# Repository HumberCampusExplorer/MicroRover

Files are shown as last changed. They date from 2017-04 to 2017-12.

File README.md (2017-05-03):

# Micro Rover
Adapted from [Rick's Trinket Rover](https://github.com/rwinscot/TrinketRover), estimated build time: 3 hours.
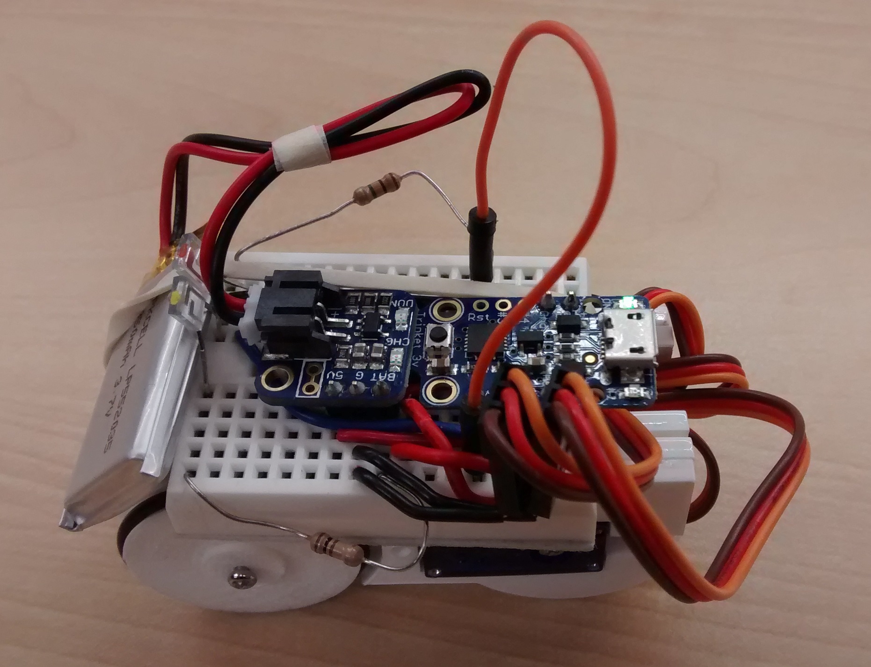
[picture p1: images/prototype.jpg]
Image of Prototype


## Table of Contents
1. [Introduction](https://github.com/six0four/MicroRover#1-introduction)
2. [Bill of Materials and Required Tools](https://github.com/six0four/MicroRover#2-bill-of-materials-and-required-tools)
3. [Instructions](https://github.com/six0four/MicroRover#3-instructions)
4. [Future Development](https://github.com/six0four/MicroRover#4-future-development)

## 1. Introduction
A common introduction to microcontrollers is through the [Lego NXT ROBOTC Curriculum](http://www.education.rec.ri.cmu.edu/previews/robot_c_products/teaching_rc_lego_v2_preview/home/ROBOTC_Curriculum_Outline.pdf). This project aims to use a low cost platform to also explore microcontrollers. Similarly, a small rover is assembled as the vehicle. Currently the small rover moves forward until an object reflects infrared light which triggers it to reverse and turn before continuing forward again.

## 2. Bill of Materials and Required Tools
For a list of materials please see the Excel file in the repository.

Regarding tools, the following are a minimum:
- Safety glasses.
- Soldering iron and lead free solder (to be added to materials list).
- Small side cutting pliers.
- Small Phillips screw driver.

## 3. Instructions
1. Soldering guidance:
	1. Start off by watching some ahort soldering guidance videos: [NASA Jove Project](https://radiojove.gsfc.nasa.gov/telescope/soldering.htm).
	2. Continue by watching some [YouTube Videos](https://www.youtube.com/watch?v=BLfXXRfRIzY&list=PLQ32vZrF5U2lFOJTtZDytBWBYVLNp4RYz).
	3. Be sure to wear safety glasses and consult an expert regarding safety, you can even start at your [local hackerspace](https://wiki.hackerspaces.org/List_of_Hackerspaces).
2. Start by programming the trinket with a blink program prior to soldering to make sure it works.
3. Soldering the headers onto to make sure trinket undamaged.
4. Upload the blink program to the trinket again to make sure it is undamaged.
6, Power the trinket from the power supply. Set the current limit.
4. Test the voltage on the 3.7 V 350 mAh Lithium Ion Polymer 552035 Cell. (Notice from the datasheet that the <a href="https://cdn-shop.adafruit.com/product-files/2750/LP552035_350MAH_3.7V_20150906.pdf">Discharge Cut-off
is 3.0V, the Charging Cut-off is 4.2V, and the Storage Voltage is 3.7-3.85V</a>)
7. Turn on the oscilloscope.
8. Turn on the funtion generator.
9. Disconnect the power supply and connect the 
5. Upload the rover code to the trinket.
6.
7.
8.

Fritzing diagrams needed
Circuit

## 4. Future Development:
- Incorporate multimeter use to check cell.
- Incorporate power supply use as a current controlled alternative to lion cell.
- Incorporate oscilloscope use to view servo motor command signal.
- Incorporate function generator use to create a test control signals.
- Serial communication http://www.ernstc.dk/arduino/tinycom.html to view digitization of infra-red sensor.
- Optimize to stay on desk.
- Optimize to seek dark spaces.
- Optimize for line following.
- Optimize to seek bright spaces and charge via a solar panel.
- Add bluetooth.
- Connect to an Android App that is also connected to Firebase.
- Re-flashing, changing, and removing boot loaders.
- Support for more operating systems.
- Support for more programming languages (Atmel AVR Assembly, ANSI C, Java, Python, IEC 61131-3, javascript, etc.).
- Support for more development environments (AVR-GCC/vi|emacs/AVRdude, Atmel Studio/Visual Studio, etc.).
- Optimize for mapping.
- Communicate with an I2C device as a master
- Communicate with an SPI device.
- Communicate with an I2C device as a slave.
- Communicate with a UART device.
- Communicate via infra-red remote codes.
- Add an H-bridge.
- Add an opto-coupler.
- Add a bidirectional level shifter.
- Modify for DC motors, optical encoders, relays.
- Modify for stepper motors (bipolar and unipolar).
- https://thewanderingengineer.com/2014/08/11/pin-change-interrupts-on-attiny85/
- PID feedback control, fan, thermistor, thermocouple.
- Function generator.
- D to A, PWM.
- A to D, filters.
- Solar cell, photo-resistor.
- Wheatstone bridge, instrumentation amplifier.
- Displays.
- De-bouncing reed switch.
- Emulate a keyboard.
- Playback sound.
- Create a custom PCB with an integrated USB port.
- Shift register, multiplexer.
- RS232, RS485.
- Add a 9-DOF IMU.
- Add MICROCHIP I2C I/O Expander MCP23017.
- Use with http://www.atmel.com/tools/atatmel-ice.aspx and http://www.microchip.com/DevelopmentTools/ProductDetails.aspx?PartNO=ATPOWERDEBUGGER
- Design shell for injection molding.
- Bar/QR code scanners, RFID, magnetic strip, fingerprint readers.
- Add SJA1000/MCP2515 for CAN.
- http://perso.uclouvain.be/fstandae/lightweight_ciphers/
- http://www.instructables.com/id/Optical-Mouse-Odometer-for-Arduino-Robot/?ALLSTEPS
- Currently the project uses a low cost, low power microcontroller from Microchip (Atmel). It could be expanded to be suitable for offerings from other companies such as:
	- Broadcom
	- National Instruments
	- Philips
	- Qualcomm (including NXP, Motorola, and Freescale)
	- Texas Instruments
	- Xilinx
	- Altera
	- Analog Devices
	- Cypress
	- Exynos (Samsung)
	- Infineon Technologies
	- Nordic Semiconductor
	- ON Semiconductor (including Fairchild)
	- Renesas Electronics (including NEC, Hitatchi, Mitsubishi)
	- SGS-THOMSON Microelectronics
	- Silicon Labs

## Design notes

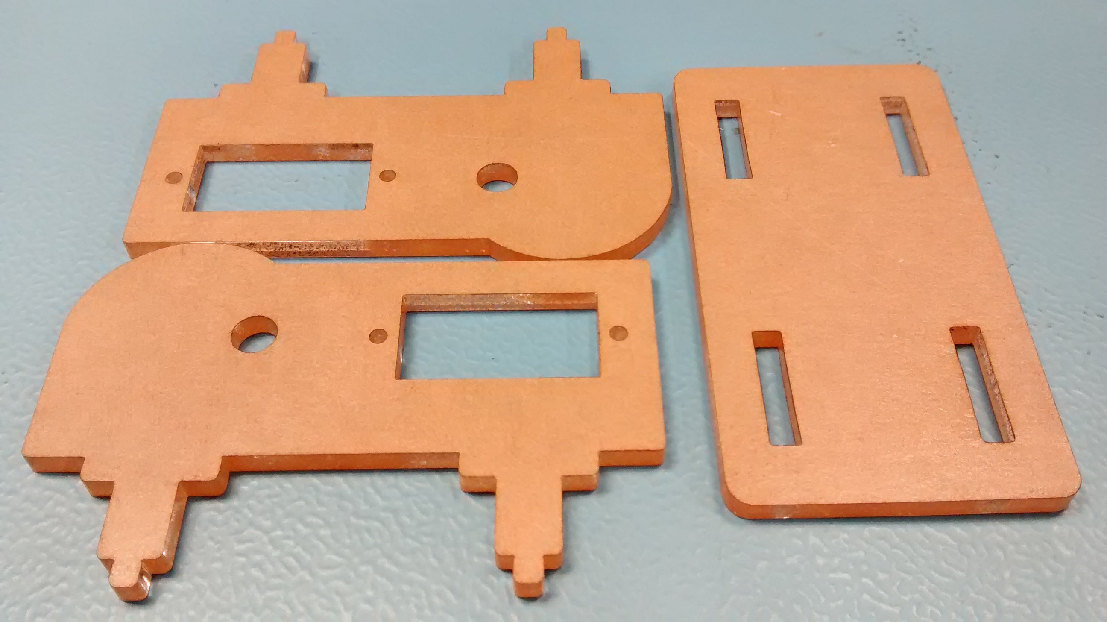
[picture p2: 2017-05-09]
images/1.13laserchassis.jpg

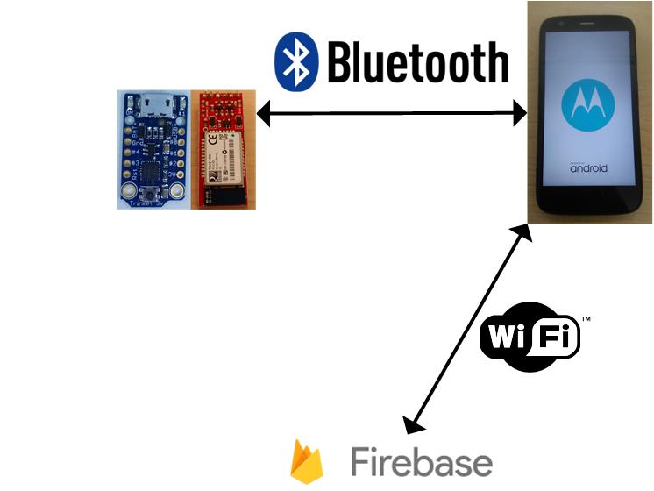
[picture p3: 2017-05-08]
images/1.3trinketnetworkarchitecture.jpg

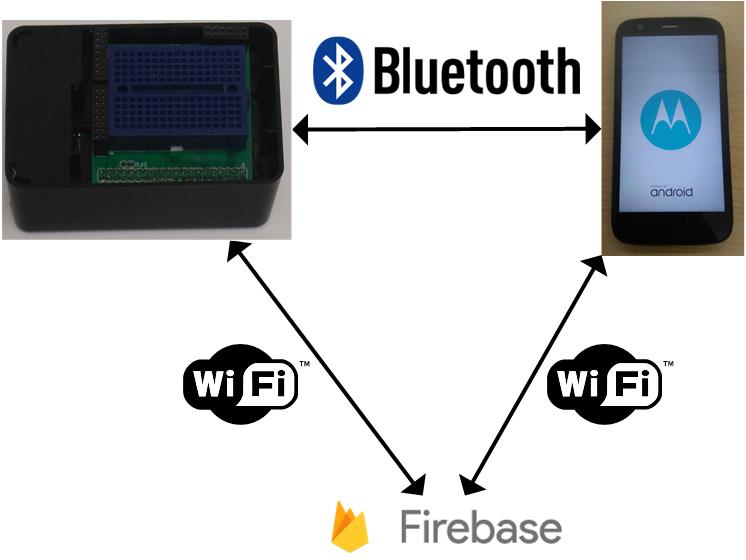
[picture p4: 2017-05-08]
images/1.2pinetworkarchitecture.jpg

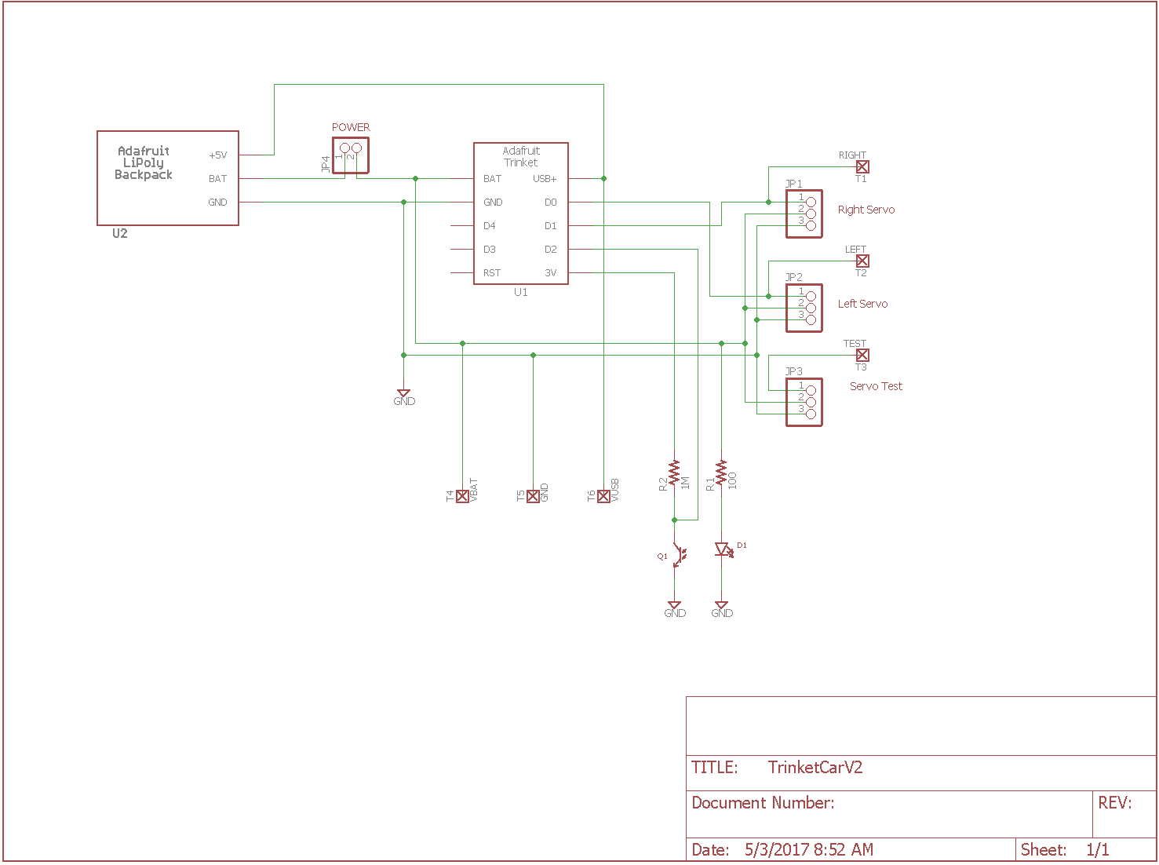
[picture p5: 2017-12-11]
electronics/TrinketCarV2_sch.png

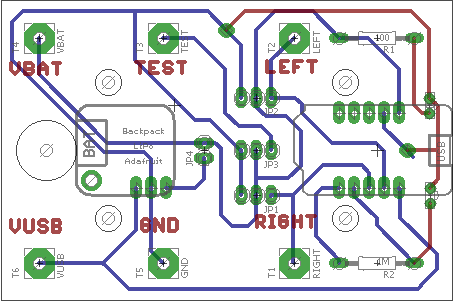
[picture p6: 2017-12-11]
electronics/TrinketCarV2_brd.png

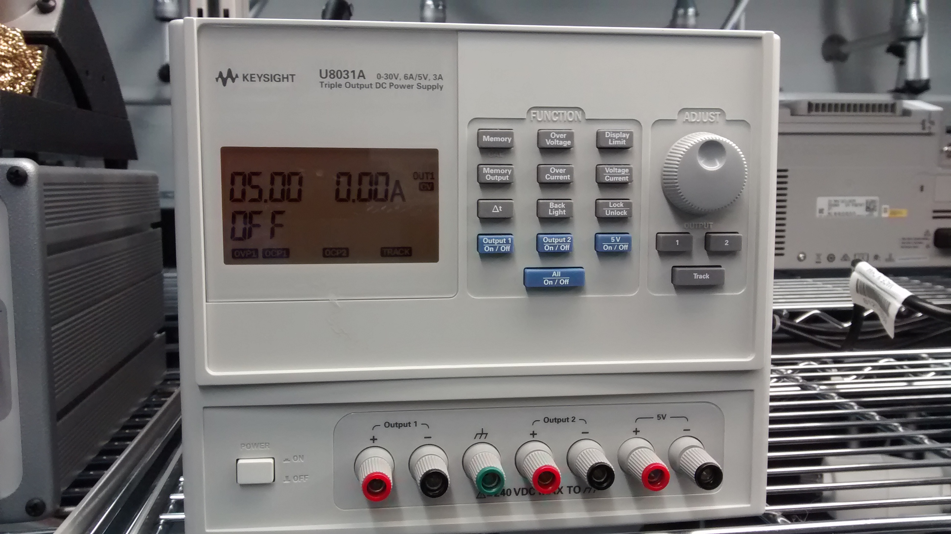
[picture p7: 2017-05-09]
images/3.13d.jpg

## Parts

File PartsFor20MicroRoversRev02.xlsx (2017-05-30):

Parts for 20 Micro Rovers
Description | Source | Part # | US$ Unit Cost | CAD$ Unit Cost | Number of units | US$ Subtotal | CAD$ Subtotal | Link | Comments
3D printed wheel for Micro Continuous Rotation FS90R Servo | 3D Hubs |  | $0.30 |  | 40 | $12.00 |  | https://www.3dhubs.com/ | Rev05 requires support while Rev02 prints without support
3D Shipping ?
3D Tax ?
Clear Acrylic 12"x24" | Johnson Industrial |  |  | $7.18 | 1.5 |  | $10.77 | http://www.johnstonplastics.com/toronto/
Acrylic cutting at a dollar per minute | Pololu, as an example |  | $1.75 |  | 20 | $35.00 |  |  | Set up fee still needs to be added, could be further optimized
Acrylic Shipping ?
Acrylic Tax ?
PCB | LPKF |  | $3.00 |  | 20 | $60.00 |  | http://docs.oshpark.com/services/ | Estimate
PCB Shipping ?
PCB Tax ?
1lb 0.032" lead free solder | Mouser | 738-13949 |  | $96.11 | 1 |  | $96.11 | 1.5 meters per project, 100 meters per spool?
Mouser Shipping ?
Mouser Tax ?
O-ring | Acklands Grainger | BS1806-022 | $0.15 |  | 40 | $6.00 |  | https://www.acklandsgrainger.com/en/product/O-RING-70BUNA-1X1-16/p/HBS568-022
Acklands Grainger Shipping ?
Acklands Grainger Tax ?
Side view IR phototransistor | Digikey | 1080-1163-ND |  | $0.481 | 20 |  | $9.62
Side View IR emitter | Digikey | 160-1930-ND |  | $0.576 | 20 |  | $11.52
100K 5% 1/4W resistor | Digikey | CF14JT100KCT-ND |  | $0.063 | 20 |  | $1.26
100 ohm 5% 1/4W resistor | Digikey | CF14JT100RCT-ND |  | $0.063 | 20 |  | $1.26
Turret Post | Digikey | 36-1502-2-ND |  | $0.352 | 120 |  | $42.19
16 Position Female Header 0.100" (2.54mm) Tin - breakaway | Digikey | S7014-ND |  | $0.746 | 22 |  | $16.41 |  | 17 pins per project needed, in addition to those with Adafruit parts
40 Position Male Header, Breakaway 0.100" (2.54mm) Gold | Digikey | S1011EC-40-ND |  | $0.967 | 6 |  | $5.80 |  | 11 pins per project needed, in addition to those with Adafruit parts
Shorting Jumper | Digikey | S9341-ND |  | $0.207 | 20 |  | $4.14
Cable A Male to Micro B Male 3.00' | Digikey | Q853-ND |  | $3.081 | 20 |  | $61.62
#2-56x1/4" machine screw | Digikey | H700-ND |  | $0.107 | 80 |  | $10.75 | note - minimum quantity 100 pcs
Digikey Shipping |  |  |  |  |  |  |  | Free shipping is offered on all orders over $100 CAD, with no additional charge for back order shipments.
Digikey Tax |  |  |  |  |  |  | $21.39
USB cable - A/MicroB - 3ft | Adafruit Product ID: | 592 | $2.95 |  | 20 | $59.00 |  | https://www.adafruit.com/product/592
36-pin 0.1" Female header - pack of 5! | Adafruit Product ID: | 598 | $2.95 |  | 2 | $5.90 |  | https://www.adafruit.com/product/598 | Not sure about numbers yet
Adafruit Trinket - Mini Microcontroller - 3.3V Logic - MicroUSB | Adafruit Product ID: | 1500 | $6.95 |  | 20 | $139.00 |  | https://www.adafruit.com/products/1500 | Eventual shift to ATtiny85 8 pin DIP
Adafruit Pro Trinket LiIon/LiPoly Backpack Add-On | Adafruit Product ID: | 2124 | $4.95 |  | 20 | $99.00 |  | https://www.adafruit.com/product/2124
Continuous Rotation Micro Servo - FS90R | Adafruit Product ID: | 2442 | $7.50 |  | 40 | $300.00 |  | https://www.adafruit.com/product/2442
Lithium Ion Polymer Battery - 3.7v 350mAh | Adafruit Product ID: | 2750 | $6.95 |  | 20 | $139.00 |  | https://www.adafruit.com/product/2750
Adafruit Shipping | UPS |  |  |  |  | $29.68 |  |  | Roughly 4% of adafruit parts cost
Adafruit Tax | 0
Total for parts from US sources |  |  |  |  |  | $884.58
Total for parts from CAD sources |  |  |  |  |  |  | $292.85
CAD$ Total for parts from all sources (using CAD$1=US$1.36) |  |  |  |  |  | $1495.87
CAD$ Total per rover |  |  |  |  |  | $74.79

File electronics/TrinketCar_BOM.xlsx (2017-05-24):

Microcar BOM
Qty | Supplier | Part Number | Description | Price@1 | Price@20 | Ext@1 | Ext@20
2 | Adafruit | 2442 | Continuous rotation micro servo | $7.500 | $7.500 | $15.00 | $300.00
1 | Adafruit | 2750 | 350mAH LiPo battery | $6.950 | $6.950 | $6.95 | $139.00
1 | Adafruit | 2124 | Pro Trinket LiPo Backpack | $4.950 | $4.950 | $4.95 | $99.00
1 | Adafruit | 1500 | 3V Trinket microcontroller | $6.950 | $6.950 | $6.95 | $139.00
1 | Digikey | 1080-1163-ND | Side view IR phototransistor | $0.660 | $0.481 | $0.66 | $9.62
1 | Digikey | 160-1930-ND | Side View IR emitter | $0.790 | $0.576 | $0.79 | $11.52
1 | Digikey | CF14JT100KCT-ND | 100K 5% 1/4W resistor | $0.160 | $0.063 | $0.16 | $1.26
1 | Digikey | CF14JT100RCT-ND | 100 ohm 5% 1/4W resistor | $0.160 | $0.063 | $0.16 | $1.26
6 | Digikey | 36-1502-2-ND | Turret Post | $0.540 | $0.352 | $3.24 | $42.19
1 | Digikey | S7014-ND | Female header - breakaway | $1.790 | $0.746 | $1.79 | $14.92
1 | Digikey | S1011EC-40-ND | Male Header - breakaway | $1.090 | $0.967 | $1.09 | $19.34
1 | Digikey | S9341-ND | Shorting Jumper | $0.340 | $0.207 | $0.34 | $4.14
4 | Digikey | H700-ND | #2-56x1/4" machine screw | $0.107 | $0.107 | $10.75 | $10.75 | note - minimum quantity 100 pcs
1 | Humber |  | Acrylic chassis kit
1 | Humber |  | Printed Circuit Board
2 | Humber |  | 3D printed wheels
 |  |  |  | ***********************************
 |  |  |  | Total Cost |  | $52.83 | $792.00
 |  |  |  | Per Unit cost |  | $52.83 | $39.60

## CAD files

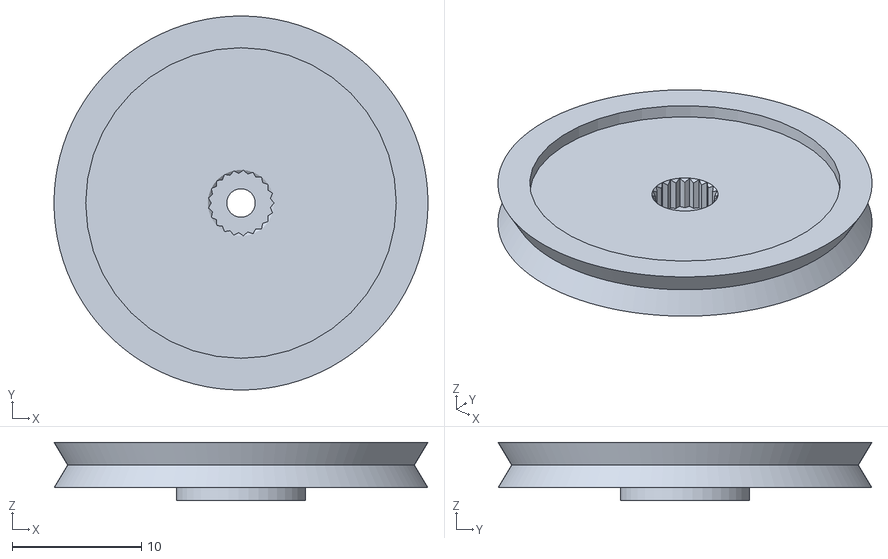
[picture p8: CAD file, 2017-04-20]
mechanical/MicroRoverOringWheelRev05.stl
28.9 x 28.9 x 4.50

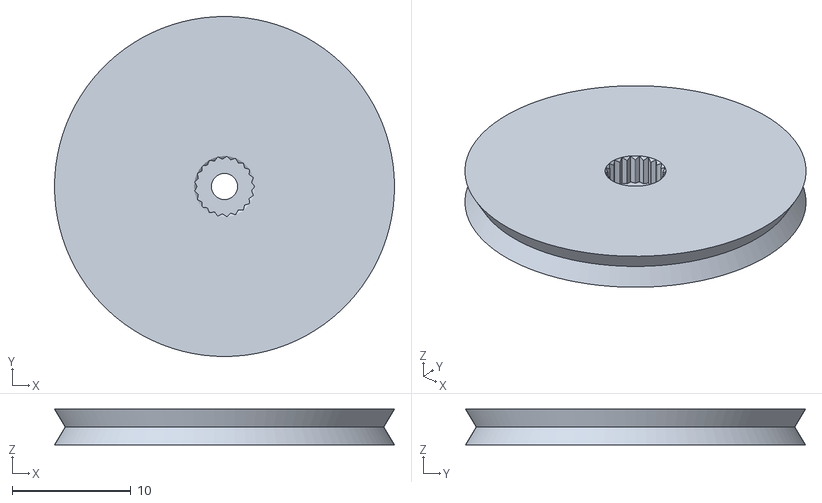
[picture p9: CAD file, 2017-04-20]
mechanical/MicroRoverOringWheelRev02bin.stl
28.6 x 28.6 x 3.00

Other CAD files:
mechanical/MicroRoverOringWheelRev02.stl
mechanical/OpenSCAD/MicroRoverOringWheelRev05.scad
mechanical/OpenSCAD/MicroRoverOringWheelRev02.scad

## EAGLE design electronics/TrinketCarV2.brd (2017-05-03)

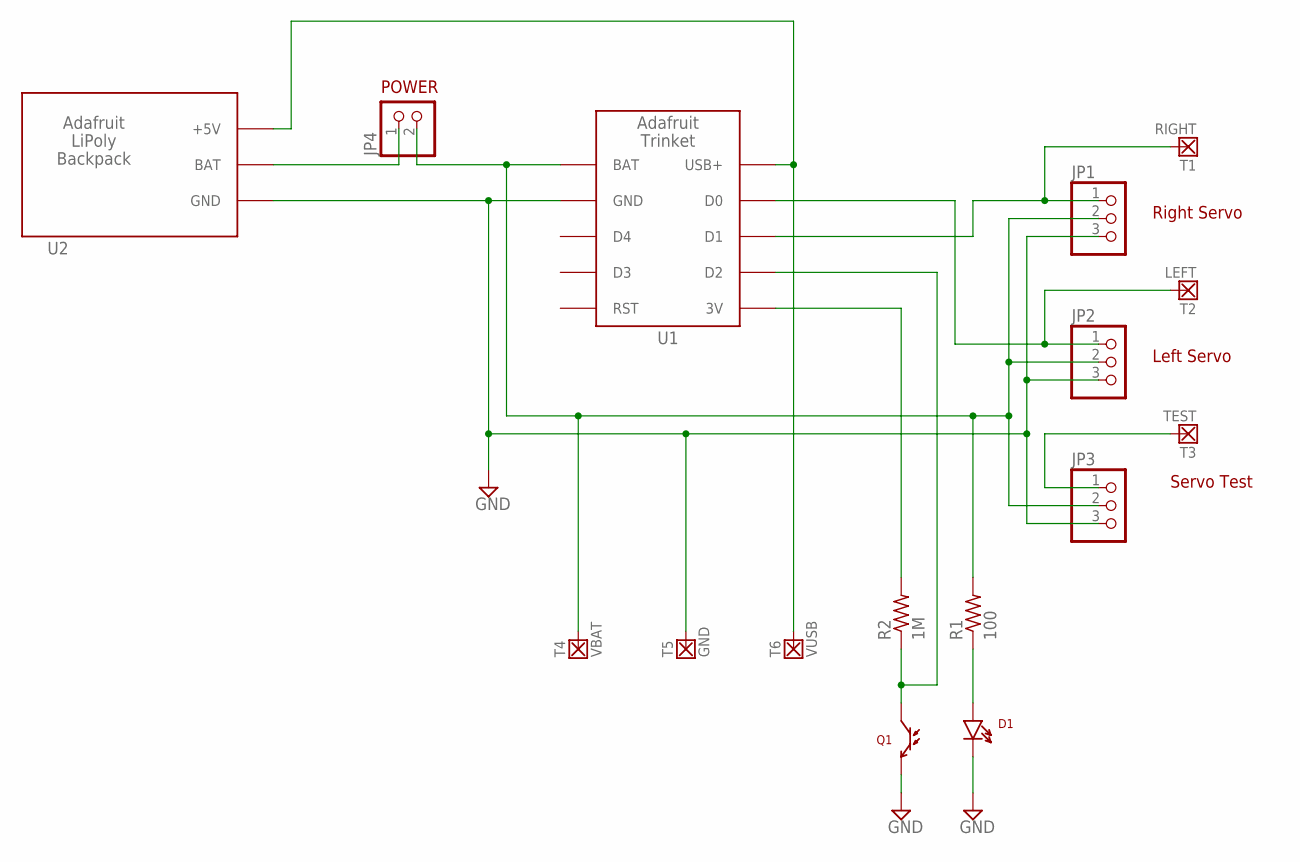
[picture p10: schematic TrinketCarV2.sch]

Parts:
D1: LTE-302
JP1, JP2, JP3: PINHD-1X3; 1X03
JP4: PINHD-1X2; 1X02
Q1: LTR-301
R1: 100; 0207/12
R2: 1M; 0207/12
T1: RIGHT; TERMPAD-SMALL
T2: LEFT; TERMPAD-SMALL
T3: TEST; TERMPAD-SMALL
T4: VBAT; TERMPAD-SMALL
T5: GND; TERMPAD-SMALL
T6: VUSB; TERMPAD-SMALL
U1: ADAFRUIT_TRINKET; TRINKITMINI
U2: LIPOLY_BACKPACK; TRINKET_LIPO_BACKPACK

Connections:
GND: D1.C, JP1.3, JP2.3, JP3.3, Q1.E, T5.P$1, U1.P$2 (GND), U2.P$2 (GND)
unnamed: R2.2, U1.P$6 (3V)
unnamed: JP4.1, U2.P$1 (BAT)
unnamed: D1.A, R1.1
unnamed: JP1.1, T1.P$1, U1.P$8 (D1)
unnamed: JP2.1, T2.P$1, U1.P$9 (D0)
unnamed: Q1.C, R2.1, U1.P$7 (D2)
unnamed: JP3.1, T3.P$1
VBAT: JP1.2, JP2.2, JP3.2, JP4.2, R1.2, T4.P$1, U1.P$1 (BAT)
VUSB: T6.P$1, U1.P$10 (USB+), U2.P$3 (+5V)

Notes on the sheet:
Left Servo
Right Servo
Servo Test
POWER

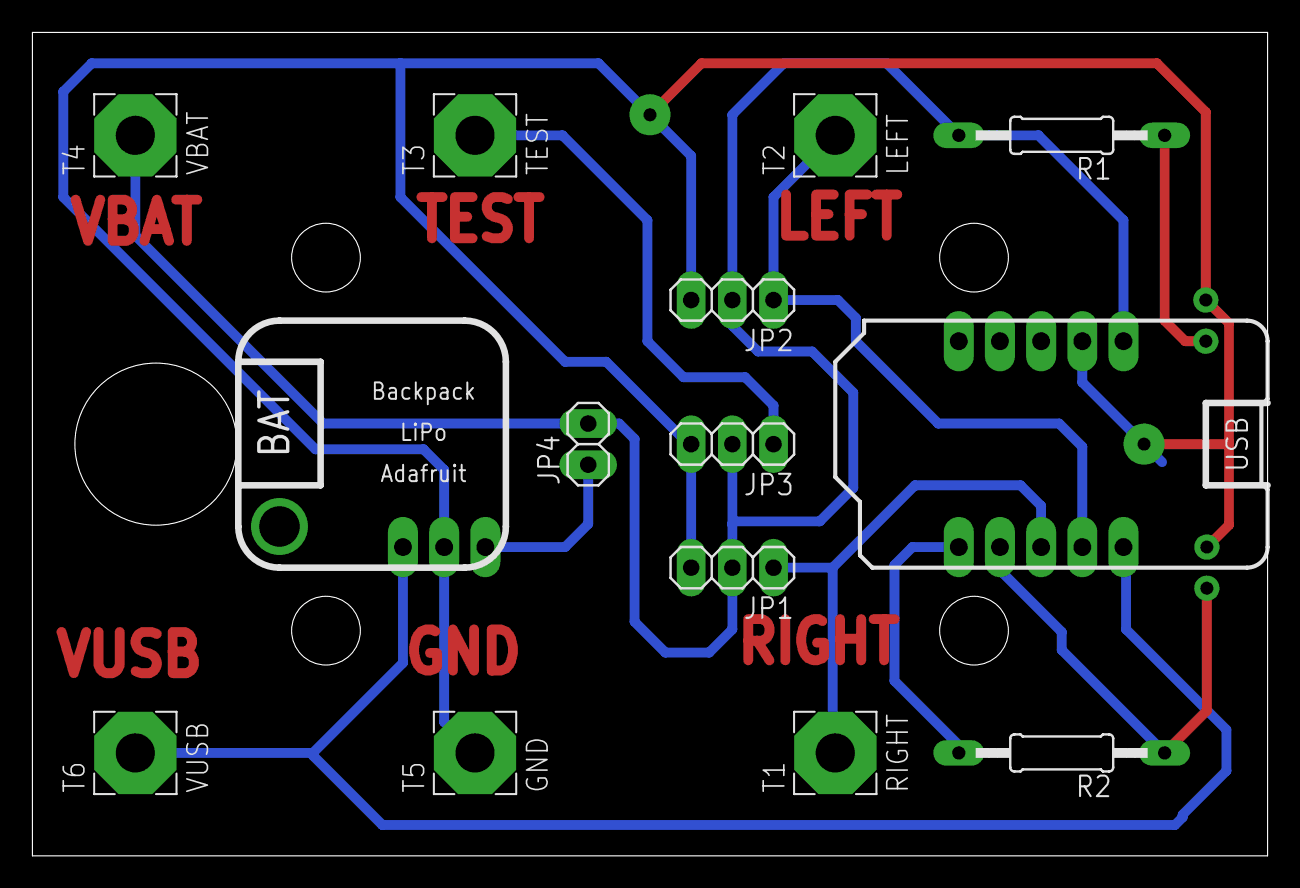
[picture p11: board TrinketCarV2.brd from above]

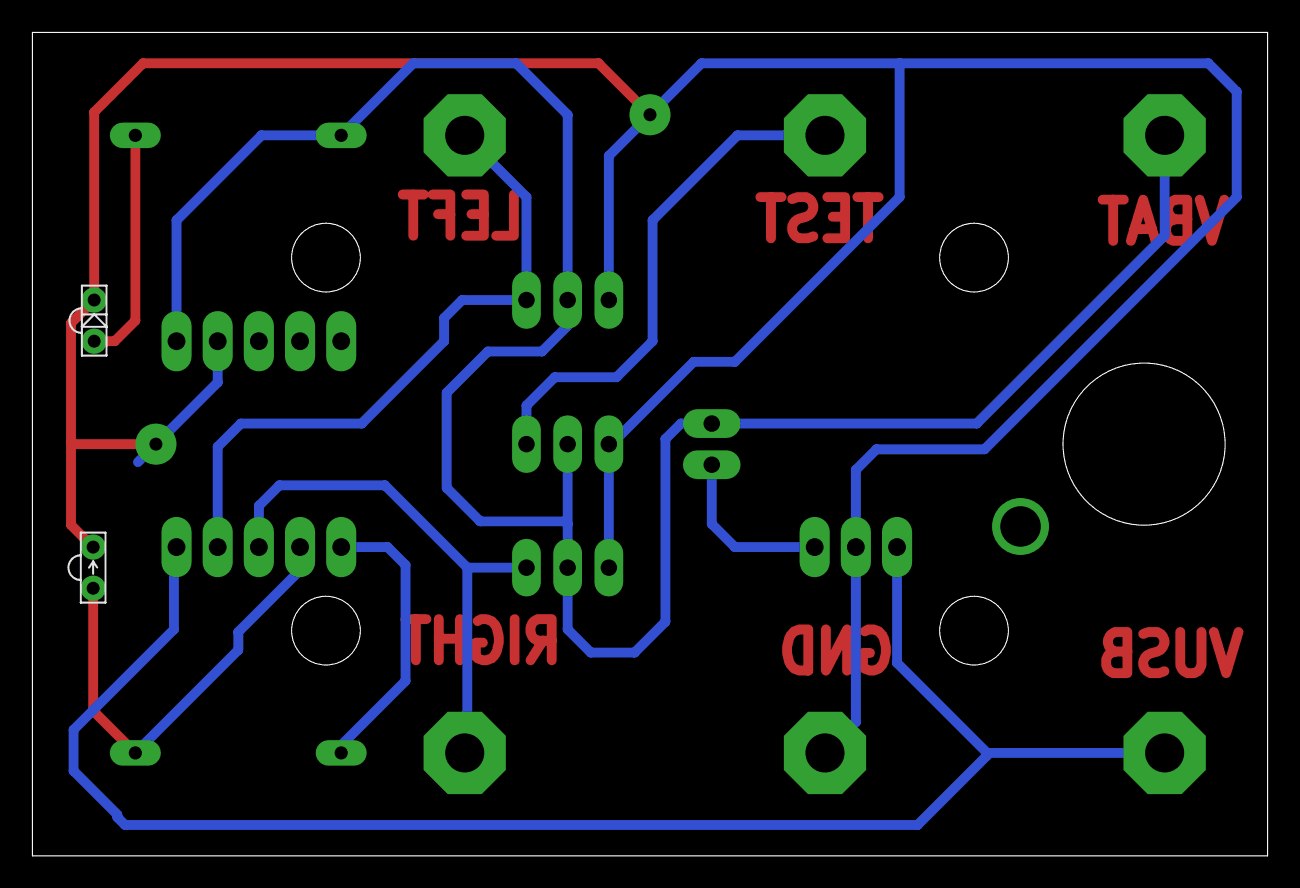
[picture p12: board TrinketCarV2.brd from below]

Board: 2 copper layers, 76.2 x 50.8 mm, 16 parts (2 on the bottom side), 10 nets.

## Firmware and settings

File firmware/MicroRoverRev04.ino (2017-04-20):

#include <Adafruit_SoftServo.h>

Adafruit_SoftServo servo_left, servo_rght;
int dis = 0;  // last measured distance
int consdis = 0; //
int adj = 0;

void setup() {

  servo_rght.attach(0); // D0
  servo_left.attach(1); // D1 = LED too
  pinMode (2, INPUT);  // D2 = A1

}

void loop() {

  dis = analogRead(1); //to read an analog voltage on pin #2, you would call analogRead(1) -> 0 to 1023
  //adj=00; //mostly forward
  //adj=50; //not sensitive enough
  //adj=70; //stops but doesn't reverse
  adj=80; //sometimes doesn't go forward especially into sunlight
  consdis=constrain((dis-500)/2.2-adj,0,180);
  if (consdis>92){
    //allow reading to set value for servos
    // Setting servos in forward motion at varying speed.
    //servo_left.write(101); // 72 reverse to 101 forward, 85 to 90 full stop
    servo_left.write(consdis);
    servo_left.refresh();
    //servo_rght.write(72); // 72 forward to 101 reverse, 85 to 90 full stop
    servo_rght.write(constrain(175-consdis,0,180));
    servo_rght.refresh();
    delay(15);
  }
  else{
    // Set servos in turn (reverse) motion instead of just stopping or straight reverse.
    for (int i = 0; i < 150; i++) {
      servo_left.write(60); //72 reverse to 101 forward: reverse quickly
      servo_left.refresh();
      servo_rght.write(95); //72 forward to 101 reverse: reverse slowly
      servo_rght.refresh();
      delay(15);  
    }
  }
}
    

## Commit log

2017-04-20 Added web framework
2017-04-20 Framework for instructions
2017-04-20 Updated 3D printed parts
    [MicroRoverOringWheelRev02.scad, MicroRoverOringWheelRev02.stl, MicroRoverOringWheelRev02bin.stl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]
2017-04-20 Showing credit to Rick and "fork"
    [MicroRoverOringWheelRev02.scad, MicroRoverOringWheelRev02.stl, MicroRoverOringWheelRev02bin.stl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]
2017-04-20 soldering links
2017-04-20 Added micro USB cable
    [PartsFor20MicroRoversRev01.xlsx]
2017-04-20 Added notes
    [PartsFor20MicroRoversRev01.xlsx]
2017-04-20 length is adequate
    [PartsFor20MicroRoversRev01.xlsx]
2017-04-21 Corrected case
2017-05-03 Added IMU
2017-05-03 Adding PCB info
    [TrinketCarV2.brd, TrinketCarV2.sch, TrinketCar_BOM.xlsx]
2017-05-04 Added wheels
2017-05-04 Starting assembly instructions
2017-05-05 Added PCB
2017-05-08 Resistor ID cards added
2017-05-08 Added link to sockets image
2017-05-08 USB cables are in!
2017-05-09 inserted USB cable image
2017-05-09 added more images for soldering clarity
2017-05-09 added chassis
2017-05-13 Adding mechanical assembly
2017-05-13 Updating mechanical assembly instructions
2017-05-14 Adding over current protection images
2017-05-14 Test euipment use is part of soldering section
2017-05-14 Over current photos linked
2017-05-14 Leads should not attached during set up
2017-05-14 Showing power connection for servo
2017-05-14 Inline images for servo power
2017-05-14 More inline images for servo power
2017-05-15 Charging with power supply
2017-05-15 Function generator, oscilloscope, and power
2017-05-15 Charging photo order improved
2017-05-15 Increase in current to not trip on servo
2017-05-24 Starting to consider a group buy
    [PartsFor20MicroRoversRev01.xlsx, TrinketCar_BOM.xlsx]
2017-05-30 Parts list updated to allow for shipping costs to be included
    [PartsFor20MicroRoversRev01.xlsx, PartsFor20MicroRoversRev02.xlsx]

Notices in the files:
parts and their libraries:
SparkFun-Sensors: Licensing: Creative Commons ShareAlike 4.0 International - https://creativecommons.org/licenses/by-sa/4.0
